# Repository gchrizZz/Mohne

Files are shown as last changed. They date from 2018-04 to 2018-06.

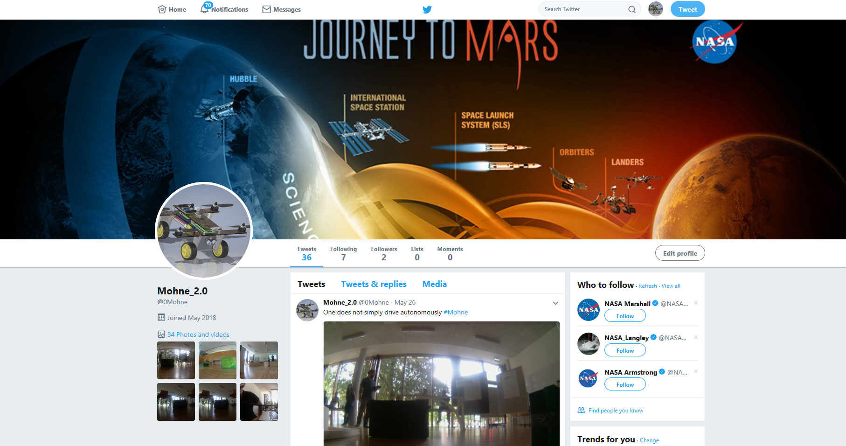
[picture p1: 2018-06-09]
01_Projektmanagement/Abschlussbericht/Screenshots/Twitter_Screenshot.PNG

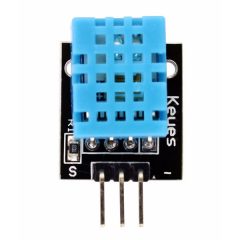
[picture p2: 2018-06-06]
04_Elektrik/KY-015_temperature_humidity_sensor_module-240x240.jpg

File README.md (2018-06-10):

# Mohne

Über dieses gitrepository können wir parallel am "Mohne für NASA" - Projekt arbeiten.

Ordnerstruktur:
- 01_Projektmanagement:  Bereich für Bericht und Organisation
- 02_Quellcode:          Bereich für die Programmierung des Quadrocopters
- 03_Konstruktion:       Bereich für die CAD-Teile des Quadrocopters 
- 04_Elektrik:           Bereich für Platinenlayouts und Circuits
- 05_Simulation:         Bereich für Circuit und Code der Simulation
- 06_Click-Dummy         Bereich für Click-Dummy für Web und App
- 99_Archiv:             Bereich für Ablage und nicht mehr relevante Artefakte

CAD Modell von Mohne:


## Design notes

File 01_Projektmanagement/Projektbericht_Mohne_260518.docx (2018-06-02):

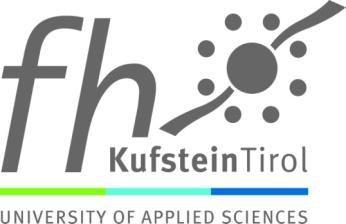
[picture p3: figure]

Project Data Explorer - Mohne

Projektbericht

Entwicklung eines Fahrzeugs für autonome/ ferngesteuerte Datenerfassung inklusive der Umweltbedingungen

Eingereicht bei:

Fachhochschule Kufstein Tirol Bildungs GmbH

Studiengang Smart Products & Solutions

Verfasser:

Anna Duregger, Christian Gruber, Christoph Jungwirth, Maximillian Möbes, Ludwig Paula, Markus Wiesmüller

Abgabedatum:

10.06.2017

# List of Figures

# Es konnten keine Einträge für ein Abbildungsverzeichnis gefunden werden.

# List of Tables

Es konnten keine Einträge für ein Abbildungsverzeichnis gefunden werden.

# List of Abbreviation

# Kurzfassung

# Abstract

# 1. Conecpt Development

Aufgrund der im letzten Semester geschaffenen Basis wurde die „Mohne“ weiterentwickelt. Alternativ gab es noch die Idee ein einfaches Auto zu konstruieren um damit die Anforderungen zu erfüllen. Letztendlich wurde die Entscheidung zugunsten der bereits gebauten Drohen getroffen und wir auf dieser Basis weiterentwickeln werden.

Für das neue Projekt wurden die folgenden Kriterien des Lektoren Teams gestellt:

- Eigenschaften des Fahrzeuges: Fahrmodus, Telemetriedaten erfassen und übertragen
- Datenerfassung: Umweltbedingungen permanent erfassen
- Digitaler Zwilling in MATLAB: Fahrzeug (mechanisches Modell-Kräfte)
- Simulation: Rapsberry Pi und Arduino Simulator
- Tracks: ferngesteuert und autonom

Die obenstehenden Punkte werden im nachfolgenden Bericht detailliert erläutert und darauf eingegangen.

## 1.1 Konzept der Fahrmodi

Die beiden Konzepte der Fahrmodi bestehen aus den Modi autonom Fahren und ferngesteuertes Fahren.

Bei der Aufgabenstellung autonomes Fahren – Obstacle Detection - sind die Anforderungen folgende:

- Eindeutige markierte Hindernisse müssen umfahren werden
- Die Hindernisse müssen abfotografiert werden
- Es werden keine Begrenzungswände verwenden
- Startpunkt lieg bei (0,0)
- Endpunkt wird vorgegeben
- Erfassen der Daten der verbauten Sensoren via ThingsSpeak und MathLab

Beim ferngesteuerten Fahren - Datenerfassung sind folgende Anforderungen:

- Startpunkt bei (0,0)
- Abfolge von Messfeldern wird je Team vorgegeben
- Hindernisse müssen umfahren werden
- Explorer wird ferngesteuert (Eingabegerät offen; Eingabe von Koordinaten, Steuerbefehle mittels Joystick)
- Erfassen der Daten der verbauten Sensoren via ThingsSpeak und MathLab

### 1.1.1 autonom

### 1.1.2 ferngesteuert

## 1.2 Fahrzeugaufbau

### 1.2.1 Elektronik

### 1.2.2 Software

# 2. Model Based Analytics

## 2.1 Digitaler Zwilling

# 3. Simulation

## 3.1 Pi Simulation

## 3.2 Arduino Simulation

# 4. Datenübertragung

## 4.1 Thinkspeak

## 4.2 Auswertung

# 5. Visualisierung MATLAB

## 5.1 Karte mit Fahrstrecke

## 5.2 Karte mit Messpunkte

## 5.3 Fahrstrecke mit Messungen

# 6. Rohdaten/Datalog

## 6.1 Timestamp+Daten

# 7. Es wird doch alles anderst als geplant

# 8. Zusammenfassung

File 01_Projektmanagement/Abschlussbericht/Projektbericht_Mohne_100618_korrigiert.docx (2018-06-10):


Project Data Explorer - Mohne

Projektbericht

Entwicklung eines Fahrzeugs für autonome / ferngesteuerte Datenerfassung inklusive der Umweltbedingungen

Eingereicht bei:

Fachhochschule Kufstein Tirol Bildungs GmbH

Studiengang Smart Products & Solutions

Verfasser:

Anna Duregger, Christian Gruber, Christoph Jungwirth, Maximillian Möbes, Ludwig Paula, Markus Wiesmüller

Abgabedatum:

10.06.2018

# List of Figures

IV

# Kurzfassung

V

Nachdem im letzten Jahr der erste Versuch gestartet war ein unbemanntes Fahrzeug auf den Mars zu schicken, ist die Mohne dieses Jahr weiterentwickelt worden. Die Aufgabe war es, das vorhandene Model weiterzuentwickeln und mit entsprechenden Modifikationen zu versehen. Dies ist in Form von Sensoren geschehen, welche Daten von der Oberfläche, der Umgebung und der Atmosphäre sammeln sollten. Damit die im ersten Projekt gestartete Idee nicht umsonst gewesen ist, wurde nach langer Diskussion entschieden, die Mohne 2.0 zu bauen. Um diese Annahme zu bestätigen, hat das Team unterschiedliche Designvarianten in Betracht gezogen. Das am Ende gewählte Design war ein sehr schlichtes und funktionales Design, welches entsprechend für die schwierigen und nicht vorhersehbaren Situationen auf dem Mars angepasst worden ist. Das Projektmanagement wurde gleich wie das im ersten Projekt (ein traditioneller Ansatz für die Gesamtplanung und für eine agile Methodik bei den Einzelaufgaben) gewählt. Um die benötigten Komponenten herzustellen – die Teile wurden überarbeitet und weiterentwickelt – konnten die Geräte im FabLab in Wattens genutzt werden. Um die Tauglichkeit für einen Einsatz auf dem Mars zu gewährleisten, mussten entsprechende Aufgaben auf einer Teststrecke bewältigt werden. Hierbei gab es einen Parcours, der mit Hilfe einer manuellen Steuerung sowie autonom befahren werden musste. Kurz vor Ende der Testphase hatten wir technische Probleme (ein notwendiges elektrisches Bauteil ist verschließen) und mussten unser komplettes Konzept innerhalb weniger Stunden den neuen Gegebenheiten anpassen und ein „neues“ Fahrzeug entwickeln.

# Abstract

VI

After last year's first attempt to send an unmanned vehicle to Mars, the Mohne has been further developed this year. The task was to further develop the existing model and provide it with appropriate modifications. This has been done in the form of sensors that should collect data from the surface, the environment and the atmosphere. So that the idea started in the first project was not in vain, after a long discussion it was decided to build the Mohne 2.0. To confirm this assumption, the team considered different design variants. The design chosen at the end was a very simple and functional design, which has been adapted accordingly for the difficult and unpredictable situations on Mars. Project management was chosen in the same way as in the first project (a traditional approach to overall planning and an agile methodology for the individual tasks). The devices could be used in the FabLab in Wattens to provide the required components - the parts were reworked and further developed. In order to ensure the suitability for a mission on Mars, corresponding tasks had to be mastered on a test track. There was a course which had to be driven with a manual control and autonomous. Shortly before the end of the test phase we had technical problems (a necessary electrical component is closed) and had to adapt our complete concept within a few hours to the new conditions and develop a "new" vehicle.

# 1. Concept Development

Aufgrund der im letzten Semester geschaffenen Basis wurde die „Mohne“ weiterentwickelt. Alternativ gab es noch die Idee ein einfaches Auto zu konstruieren um damit die Anforderungen zu erfüllen. Letztendlich wurde die Entscheidung zugunsten der bereits gebauten Drohne getroffen, die das Projektteam auf dieser Basis weiterentwickeln wird.

Für das neue Projekt wurden die folgenden Kriterien des Lektoren Teams gestellt:

- Eigenschaften des Fahrzeuges: Fahrmodus, Telemetrie Daten erfassen und übertragen
- Datenerfassung: Umweltbedingungen permanent erfassen
- Digitaler Zwilling in MATLAB: Fahrzeug (mechanisches Modell-Kräfte)
- Simulation: Raspberry Pi und Arduino Simulator
- Tracks: ferngesteuert und autonom

Die obenstehenden Punkte werden im nachfolgenden Bericht detailliert erläutert und besprochen.

## 1.1 Konzept der Fahrmodi

Die beiden Konzepte der Fahrmodi bestehen aus den Modi autonom Fahren und ferngesteuertes Fahren.

Bei der Aufgabenstellung autonomes Fahren - Obstacle Detection - sind die Anforderungen wie folgt:

- Eindeutige markierte Hindernisse müssen umfahren werden
- Die Hindernisse müssen abfotografiert werden
- Es werden keine Begrenzungswände verwendet
- Startpunkt lieg bei (0,0)
- Endpunkt wird vorgegeben
- Erfassen der Daten der verbauten Sensoren via ThingsSpeak und MATLAB

Beim ferngesteuerten Fahren - Datenerfassung gibt es folgende Anforderungen:

- Startpunkt bei (0,0)
- Abfolge von Messfeldern wird je Team vorgegeben
- Hindernisse müssen umfahren werden
- Explorer wird ferngesteuert (Eingabegerät offen; Eingabe von Koordinaten, Steuerbefehle mittels Joystick)
- Erfassen der Daten der verbauten Sensoren via ThingsSpeak und MATLAB

### 1.1.1 Autonom

Um den Parcours autonom zu absolvieren wurden zusätzliche Sensoren verwendet, mit denen diese Aufgabe vereinfacht wird. Zum einen wurde ein Gyroskop angeschlossen um die Orientierung im Raum zu vereinfachen. Zum anderen ein Ultraschallsensor damit Hindernisse erkannt werden können.

Für die Programmierung wurde der Raspberry Pi und der Arduino verwendet. Auf dem Arduino ist die Motorsteuerung gespeichert und auf dem Pi die Kamerafunktion und der Array. Beide Computer kommunizieren mithilfe einer i2c-Verbindung und senden Zahlen hin und her, welche die verschiedene Funktionen auslösen. Das autonome Fahren beim Auto konnte leider nicht komplett absolviert werden, da das Auto selber nicht in einer Linie fährt, sondern eine Rechtsneigung besaß. (defekter Reifen) Es fuhr so lange vorwärts, bis sich ein Hindernis 30 Zentimeter vor dem Fahrzeug befindet. Dieser Wert wird mit einem Ultraschallsensor berechnet. Dieser ist am Arduino angeschlossen und muss dem Raspberry Pi mitteilen, dass ein Hindernis vorhanden ist und ein Foto gemacht werden muss. Durch die i2c-Verbindung wird vom Arduino die Zahl 7 versendet. Das Problem hierbei ist, dass der Arduino nicht von sich aus in der Slave Konfiguration Zahlen senden kann. Somit muss der Raspberry Pi regelmäßig den Arduino fragen, ob ein Hindernis vorhanden ist. Diese Frage wird mithilfe einer Zahl jede Sekunde gestellt und geantwortet wird mit einen von zwei Zahlen. Entweder ist ein Hindernis vorhanden oder die Bahn ist frei. Nachdem der Raspberry Pi die Antwort erhalten hat, wird entsprechend gehandelt. Bei einem Objekt wird die Kamerafunktion ausgelöst und das Bild wird auf Twitter geladen. Nachdem das Foto geschossen wurde, wird eine Rechtskurve gefahren und das Auto fährt weiter.

Die Motorsteuerung wurde aus dem 1. Projekt im 1. Semester übernommen und angepasst. Um Platz auf dem Breadboard und Pins auf dem Arduino zu sparen wurde nur eine H-Brücke gebaut und die linken bzw. rechten Reifen parallelgeschaltet. Da die Motoren sehr schwach sind, wurde immer der höchste Wert von 255 verwendet. Bei den Links- und Rechtsdrehungen wird wie ein Panzer gefahren. Das heißt, dass beide Seiten sich gegeneinander bewegen, bis sich das Auto in einem Winkel von 90 Grad gedreht hat.

### 1.1.2 Ferngesteuert

Bei der Aufgabe das Fahrzeug über den Parcours per Fernsteuerung zu fahren gibt es viele Möglichkeiten die Fernsteuerung zu kreieren. Wir haben uns dann schlussendlich für die Laptoptastatur entschieden. Dies hat den Vorteil, dass jeder den Code testen kann ohne eine physische Fernsteuerung mitnehmen zu müssen und falls es Probleme bei der Verbindung gibt, kann die Mohne per Not-Stopp ausgeschaltet werden. Da das Fahrzeug bereits mit einem Samba Server verbunden ist war die Remote-Steuerung leicht zu verwenden und in der Testphase konnten die verschiedenen Programme schnell verändert werden. Der Code für die Fernsteuerung heißt ‚FernFoto.py‘ und kommt von ‚Fernsteuerung‘ und ‚Foto‘.

Die Motorsteuerung war auf dem Arduino gespeichert. Dies war bei der ursprünglichen Mohne, wie auch bei unserem endgültigen Auto der Fall. Auf die Motorsteuerung selber wurde bereits im Abschnitt Autonom eingegangen.

Der Code für die Fernbedienung wurde auf dem Raspberry Pi mithilfe eines Keyloggers geschrieben. Der verwendete Logger kommt aus der pynput Library. Dies hatte den Vorteil, dass es auch eine Key Release Funktion gab und dadurch die Mohne stoppt, wenn eine Taste losgelassen wurde. Der Nachteil war allerdings, dass der Keylogger nicht zusammen mit Schleifen funktioniert. Somit konnte der Raspberry Pi nicht selbständig Fotos schießen. Dieses Problem wurde gelöst indem ein separater Tastendruck die Kamera auslöst und das Bild auf Twitter hochgeladen wird.

Die Mohne wird klassisch mit den Pfeiltasten gesteuert. Beim Drücken der Leertaste entsteht das Foto und mit der Escape-Taste wird das Programm gestoppt. Wenn keine Taste gedrückt wird oder eine losgelassen wird, werden die Motoren ausgeschaltet.

Jetzt müssen die Befehle nur noch an den Arduino geschickt werden, um diese auszuführen Die im Unterricht gelernte i2c-Verbindung wurde verwendet und modifiziert. Jede Taste wurde einer Zahl zugeordnet, die an den Arduino geschickt wird. Wenn die Motoren stoppen sollen wird auch eine Zahl gesendet.

Der Code auf dem Arduino heißt ‚Fern_1.0‘. Auf diesem wurden bereits Klassen für die jeweiligen Richtungen geschrieben. Also vorwärts, rückwärts, rechts und links. Dazu natürlich noch die Stopp Funktion. Durch die i2c-Verbindung wartet der Arduino auf die Zahlen, welche vom Raspberry Pi gesendet werden. Bei der Zahl 1 wird nach vorne gefahren, bei der 2 nach rechts. Wird die 3 gesendet nach Links und bei der 4 rückwärts. Die Nummer 5 wird für die Stopp-Funktion verwendet.

Die Fernsteuerung lief trotz vielen Schnittstellen sehr präzise und ohne Verzögerung.

## 1.2 Fahrzeugaufbau

### 1.2.1 CAD als Unterstützung für die Fertigung und Designentwicklung

Die Mohne besteht aus 66 Einzelteilen. Kabel, Schrauben, Muttern und Kabelbinder sind hierbei nicht berücksichtigt.

In Abbildung 1 ist das fertige CAD Modell als Explosionsdarstellung aufgezeigt, um die Komplexität des Modells zu veranschaulichen.

Ohne ein ausgereiftes CAD-Modell ist eine ordnungsgemäße Fertigung der Mohne nicht möglich. Außerdem hilft das digitale Modelle etwaige Lücken bzw. Versäumnisse in der Konzeption aufzudecken, noch bevor eine zeitintensive Fertigung gestartet wird.

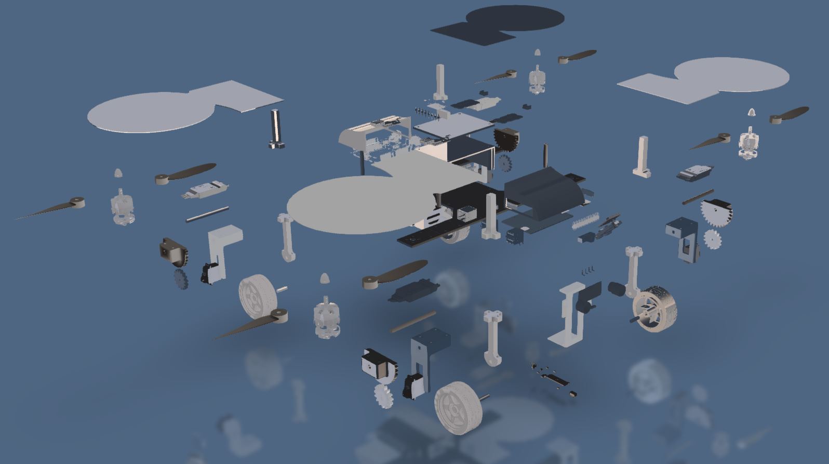
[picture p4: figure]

Abbildung 1: Explosionsdarstellung Mohne

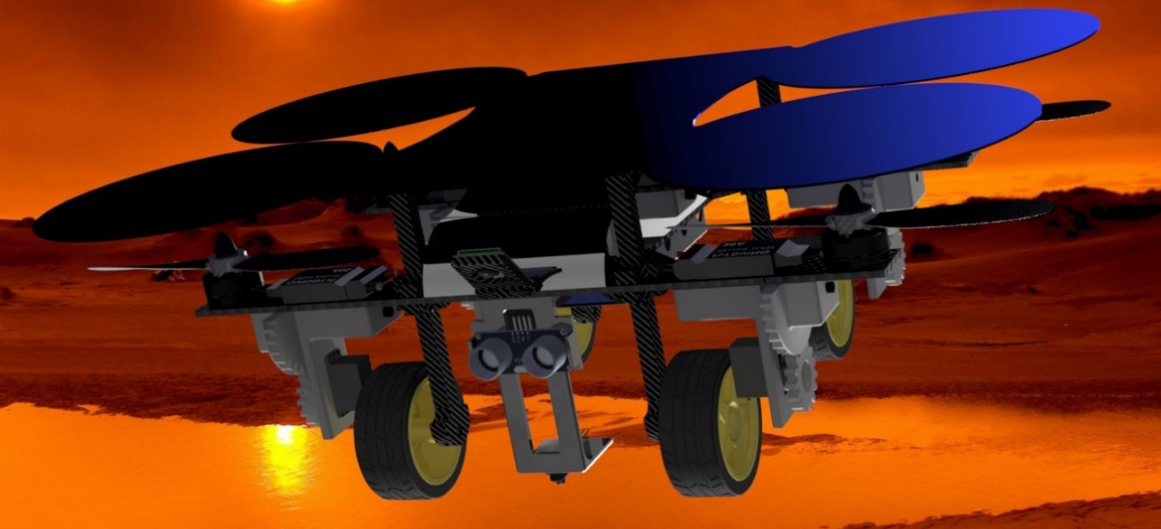
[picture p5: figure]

Abbildung 2: Rendering Ansicht Mohne

Abbildung 2 zeigt ein Rendering Bild der auskonstruierten Mohne. Im Zuge der Designentwicklung wurden folgende vier Designschwerpunkte hinsichtlich der NASA als Kunde getroffen:

1. Entwicklung eines individuellen und additiv gefertigten Gehäuses zum Schutz der Steuergeräte
2. Modulares Sensorplattenkonzept, welches einen Wechsel durch reine Schraub- und Steckverbindungen ermöglicht
3. Einsatz von Kohlefaser als modernes, vielseitiges und gewichtsoptimiertes Material
4. Solarmodule zum Laden des Akkumulators

Das gesamte CAD Modell und das Designkonzept kann unter https://github.com/gchrizZz/Mohne abgerufen werden.

### 1.2.2 Elektronik

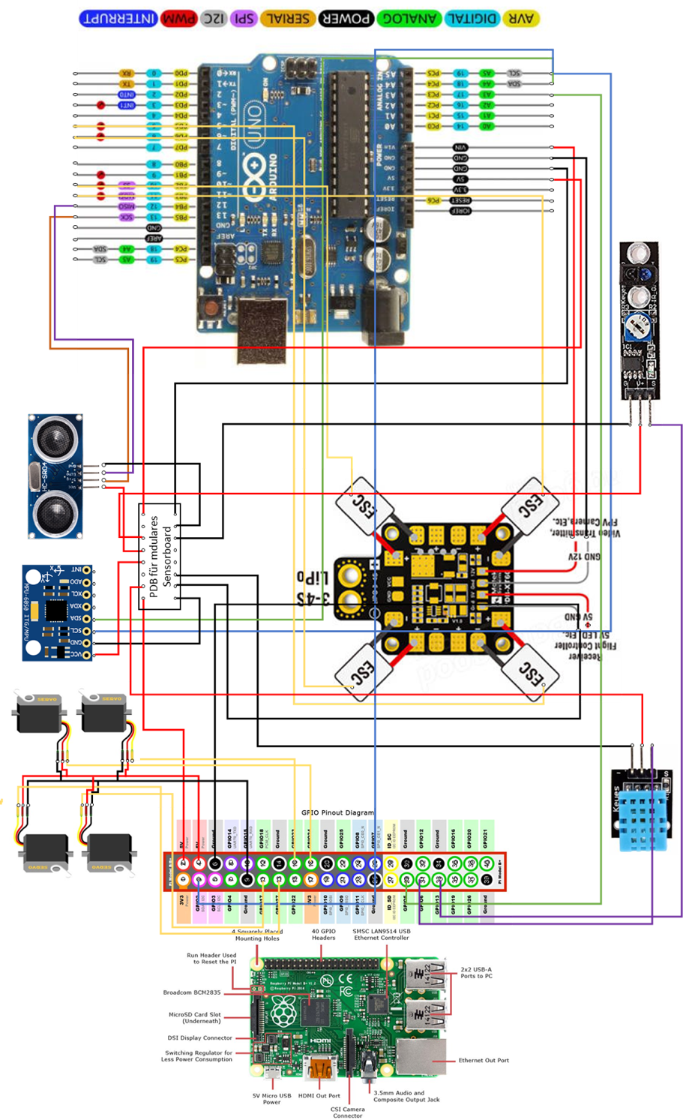
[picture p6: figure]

Abbildung 3: Elektronische Komponenten und Verkabelung Mohne

Abbildung 3 zeigt den Kabelbaum und die elektrischen Komponenten der Mohne auf. Dieser Plan berücksichtigt lediglich die geforderten Sensoren, dennoch ist die Designentscheidung einer modularen Sensorplatte bereits einkalkuliert. Hierfür wurde ein gesondertes PDB ausschließlich für die Stromversorgung aller angebrachten Sensoren eingearbeitet. Somit müssen zusätzliche Sensoren lediglich an diesem PDB und mit Ihren Signalkabeln an das vorgesehene Steuergerät (Pi oder Uno) angeschlossen werden. Löten ist nicht mehr notwendig.

### 1.2.3 Kommunikation

Der Zugriff der Mohne wird nach wie vor über einen Samba Server realisiert. Samba ist ein freies Programmpaket, das es ermöglicht, Windows-Funktionen wie die Datei und Druckdienste unter anderen Betriebssystemen zu nutzen und die Rolle eines Domain Controllers anzunehmen. Es implementiert hierfür unter anderem das Server Message Block/Common Internet File System-Protokoll (SMB/CIFS-Protokoll). Im Projekt wurde Samba als DC und DNS verwendet, damit man via RDP über WLAN auf den Raspberry Pi zugreifen kann, ohne eine statische IP hinterlegen zu müssen. Der Hostname der Drohne lautet „Mohne“.

Die Kommunikation zwischen dem MPU, dem Arduino Uno und dem Pi wurde via I²C realisiert. I²C (gesprochen "I quadrat C") ist ein synchroner, serieller Zweidraht-Bus, der jeweils eine bidirektionale Daten- und Taktleitung verwendet und für die Kommunikation zwischen ICs über kleine Distanzen geeignet ist. Die Bezeichnung steht für IIC, Inter-Integrated Circuit.

Der Kombi-Sensor (KY-015), als auch der Linetracking Sensor (KY-033) sind mittels jeweils einem GPIO Pin mit dem Pi verbunden. Somit können die Daten von diesen direkt über das digitale Eingangssignal am Pi verarbeitet werden.

Da die Logikverarbeitung für das autonome Fahren hinsichtlich Linetracking und Orientierung in einem Schachbrett-Array auf dem Pi abläuft, kann man mit dieser einfachen und direkten Kommunikation die Logik am leichtesten realisieren.

Die Servos, welche für die Ausrichtung der Motorhalterung an allen vier Armen der Drohne verantwortlich sind, werden ebenfalls via GPIO Pins an den Raspberry Pi angebunden. Jedoch wird diesen ein imitiertes PWM Signal gesendet, um sie zu steuern.

Der Ultraschallsensor (USS) ist mittels zwei IO Pins direkt am Arduino angeschlossen. Auf diesem Weg kann die unmittelbare Hinderniserkennung am schnellsten realisiert werden. Da der USS ausschließlich mit dem Arduino Uno kommuniziert, muss die Logikverarbeitung hierfür im C++ Code auf dem Arduino stattfinden.

## 1.3 Model Based Analytics

Der Grundgedanke von Model Based Analytics ist die virtuelle bzw. digitale Darstellung eines physischen Modells. Dieses Modell wird in der digitalen Welt analysiert und interpretiert. Dies ist eine Methode gewisse Problemstellungen virtuell darzustellen und diese als Simulation zu verwenden.

Für unser Projekt wurde der Digitale Zwilling gewählt um diese Problemstellung darzustellen und eine entsprechende Lösung zu finden.

## 1.4 Digitaler Zwilling

Das Konzept eines digitalen Zwillings besteht aus drei Elementen: einem physischen Zwilling in der realen Welt, einem digitalen Zwilling im virtuellen Raum, der sowohl alle alten betrieblichen Daten als auch die Echtzeitdaten des physischen Zwillings abbildet, und die Interkonnektivität, die es den Zwillingen ermöglicht, die Informationen auszutauschen. Digitale Zwillingen können für Simulationen verwendet werden und für Einblicke in den arbeitenden Zwilling, um Prozesse zu überwachen und mögliche Fehler zu entdecken.[^1]

Im folgenden Abschnitt werden nähere Beschreibungen zum digitalen Zwilling angeführt.

### 1.4.1 Allgemein

Ein digitaler Zwilling ist eine virtuelle Modellbildung zum Beispiel eines Prozesses, eines Produkts oder einer Dienstleistung, welches die reale und virtuelle Welt verbindet. Digitale Zwillinge verwenden reale Daten von installierten Sensoren, welche die Arbeitsbedingungen oder Position von Maschinen repräsentieren. Diese Kopplung der virtuellen und realen Welten ermöglicht die Analyse von Daten und die Überwachung von Systemen, um Probleme verstehen und bearbeiten zu können, bevor sie überhaupt auftreten. Ausfallzeiten können frühzeitig vermieden werden und dadurch neue Chancen entwickeln und mithilfe von Computersimulationen, damit die Zukunft besser geplant werden kann. Heutzutage werden digitale Zwillinge eine geschäftliche Notwendigkeit, weil der gesamte Lebenszyklus eines Produkts, Prozesses oder Geschäftsmodells abdeckt werden kann und somit die Grundlage für verbundene Produkte und Dienstleistungen bilden.

Für den sogenannten digitalen Zwilling sind folgende Anforderungen notwendig: das abzubildende reale Objekt, den digitalen Zwilling im virtuellen Raum und Informationen, welche die beiden miteinander verbinden. Digitale Zwillinge können dadurch die operative und auch finanzielle Leistungsfähigkeit eines Objekts wie einer Anlage oder einer Dienstleistung verbessern und in Echtzeit dargestellt werden.

In der ersten Phase „Design“ geht es um den Umgang mit komplexen Produktanforderungen, schnellen Entwicklungszyklen und strengen regulatorischen Anforderungen. In der zweiten Phase „Erstellung (manufacturing)“ kann der Zwilling helfen, bessere Effizienz, Qualität und höheren Ertrag in der Erstellung zu erreichen. In der dritten Phase „Nutzung (operate)" kann ein digitaler Zwilling u. A. eingesetzt werden, um die Verfügbarkeit von Objekten (z. B. Maschinen) zu verbessern. In der vierten Phase „Wiederverwertung (Recycling)“ kann der digitaler Zwilling z.B. für die Ersatzplanung oder der Eruierung von Upcycling-Potenzialen eingesetzt werden.

### 1.4.2 Projektbezogen

Unser Plan B des Projektes Data Explorer wurde an einem Tag zu einem Auto umgebaut und deren Funktionen erweitert bzw. ergänzt. Am Auto herrscht ein mechanisches Kräftemodell, welches im folgenden Kapitel dargestellt wird. Dadurch haben wir entschieden, dass wir die Kraft des Motors mit der Beschleunigung als Digitalen Zwilling modellieren bzw. darstellen wollen. Interessant an der Darstellung wird, wie sich die Beschleunigung „a“ während der Datenerfassung verhält. Die Erfassung der Daten erfolgt mithilfe der Matlab Software und dessen Mobile App. Durch die Kommunikation zwischen den beiden Anwendungen kann eine Erfassung der Daten mit verschiedenen Sensoren, wie Beschleunigungssensor, erfasst werden. Es kann analysiert werden, ob bei der Absolvierung des vorgegebenen Parcours eine Verminderung der Beschleunigung eintritt, wenn ein Hindernis kommt oder eine Kurve nach links oder rechts gemacht wird. Der digitale Zwilling wird in einem Plot der Matlab Software dargestellt, damit das Diagramm entsprechend erläutert und interpretiert werden kann.

### 1.4.3 Material und Methoden

Für die Erfassung des digitalen Zwillings unseres Sommerprojektes haben wir uns entschieden, dass wir die Anwendung der Matlab App verwenden werden, da wir kein Logfile über den Raspberry Pi erstellen. Für die Anwendung ist die Matlab Software und der Download der dazugehörigen Matlab Mobile App notwendig. Zu Beginn wird die Matlab Mobile App am Smartphone installiert, egal ob Android oder iOS Betriebssystem. Am Smartphone können die unterschiedlichsten Sensoren wie Beschleunigungs-, Magnetfeld-, Positions-, Winkelgeschwindigkeits- und Orientierungssensor aktiviert werden. In der Software ist eine Installation eines Add-Ons zu erledigen. Um eine Verbindung zwischen der Software und der App herzustellen, wird in der Kommandozeile der Software der Konnektor aktiviert. Es wird nun die funktionierende IP-Adresse angezeigt, welche im Smartphone eingegeben wird, um eine Kommunikation herstellen zu können. Als nächsten Schritt wird der Link von PC und Smartphone erzeugt und es können sowohl am Smartphone und in der Kommandozeile durch bestimmte MATLAB-Befehle die Sensoren aktiviert werden. Für eine korrekte Datenerfassung werden durch Befehle in der Kommandozeile die Datenaufnahme der Messwerte aktiviert und auch wieder beendet. Mit den erfassten Sensordaten des Smartphones können die Daten auf verschiedensten Arten analysiert und auch dargestellt werden. Die Daten können in einem Diagramm inklusiver Legende in MATLAB dargestellt werden.

### 1.4.4 Mechanisches Modell des Fahrzeuges

Im folgenden Bild wird das mechanische Modell unseres Fahrzeuges abgebildet. Das Kräftemodell des Fahrzeuges besteht aus der Reibungskraft, der Erdanziehungskraft, der Kraft des Motors in der Vorwärtsbewegung und der Kraft des Autos.

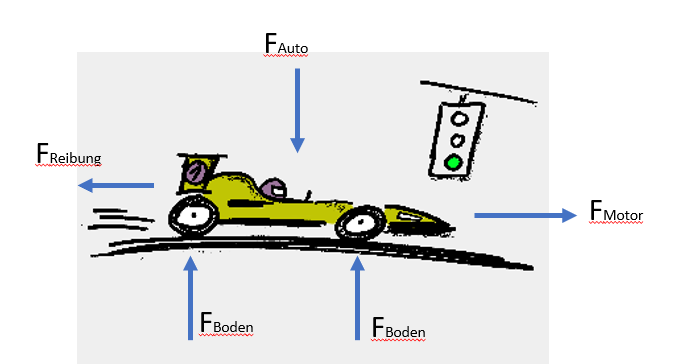
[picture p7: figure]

Abbildung 4: Mechanisches Kräftemodell des Autos

### 1.4.5 Ergebnisse

Aus der Datenerfassung der Matlab App konnte die Kraft des Motors erfasst und gemessen werden. Die Daten wurden während unseres autonomen Fahrens, welches leider in der kurzen Zeit nicht möglich war fertig zu programmieren, aufgenommen. Anhand der Daten, die auf die Software von Matlab übertragen wurden, kann herausgelesen werden, dass unser Programm eine relativ kontinuierliche Geschwindigkeit durchfährt. Daraus resultiert, dass unser Fahrzeug, wegen dem nicht fertigen ferngesteuertem Programm, nicht immer Objekte bzw. Hindernisse erkennen kann und somit sich nicht mit einer kontinuierlichen Geschwindigkeit fortbewegt.

Mit der Darstellung der Beschleunigung ist keine kontinuierliche Beschleunigung ersichtlich. Der programmierte Code enthält leider keine konkrete Struktur bzw. Abfolge und somit resultiert ein relativ hektisches Beschleunigungsdiagramm. In der Mitte des Diagramms kann man erkennen, dass das Fahrzeug einen Stillstand hat und womöglich ein Hindernis erkennen konnte.

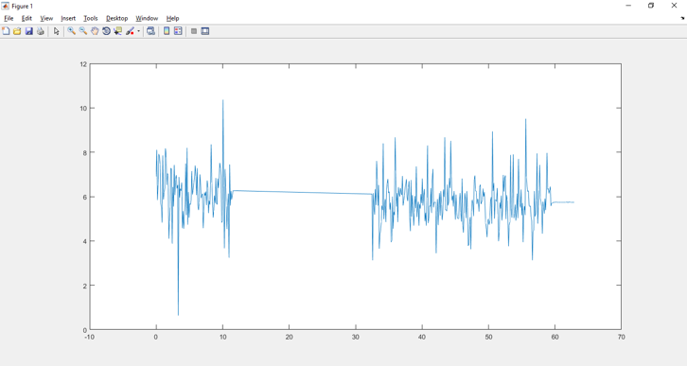
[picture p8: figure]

Abbildung 5: Diagramm für die Beschleunigung

Im folgenden Plot von Matlab ist die Winkelgeschwindigkeit dargestellt. Auf dieser Darstellung erkennt man wie sich das Fahrzeug in den Richtungen verändert. Wie schon vorher erläutert haben wir den Fernsteuerungsmodus leider nicht bis zum Ende programmieren können. Im Diagramm ist schön zu sehen, wie oft und schnell das Fahrzeug die Richtung ändert. Das ist der Grund, dass das Programm nicht in der Zeit fertig geworden ist. Deswegen fährt das Fahrzeug willkürlich durch den Raum und während der Gerade des Diagramms hat es angehalten, weil es womöglich ein Hindernis erkannt hat. Ursprünglich ist es gedacht, dass das Fahrzeug einem Hindernis ausweicht, jedoch nach dem Diagramm sind auf unserem vorgegebenen Parcour sehr viele Hindernisse platziert worden.

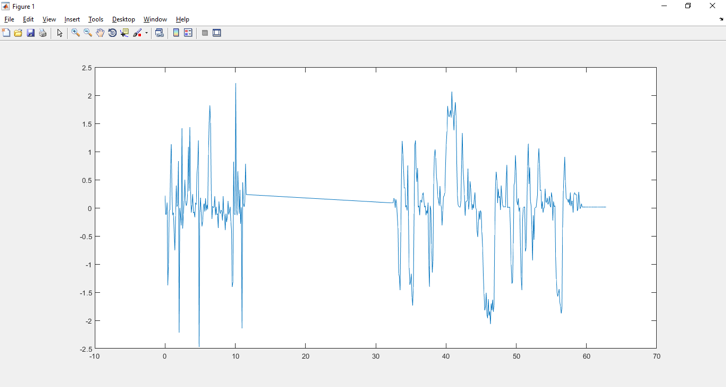
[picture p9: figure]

Abbildung 6: Diagramm für die Winkelgeschwindigkeit

### 1.4.6 Konklusion

Am Beispiel der beiden Diagramme kann man erkennen, dass unser programmierter Quellcode leider nicht dem Fernsteuerungsmodus entspricht. Das Fahrzeug kann durch die Bilderkennung nicht kontinuierlich die Hindernisse erkennen und daraufhin die Geschwindigkeit reduzieren bzw. nach dem Stillstand wieder beschleunigen. In der Mitte des Diagramms ist ein Stillstand zu erkennen, weil hier womöglich ein Hindernis erkannt wurde. In beiden Abbildungen ist die Beschleunigung als auch die Winkelgeschwindigkeit sehr hektisch, da das Programm aus zeitlichen Gründen nicht fertig geschrieben werden konnte.

# 2. Simulation

Simulation ist die Nachahmung des Betriebs eines realen Prozesses oder Systems. Der Akt der Simulation erfordert zunächst die Entwicklung eines Modells, das die wesentlichen Merkmale, Verhaltensweisen und Funktionen des gewählten physikalischen oder abstrakten Systems oder Prozesses darstellt. Das Modell stellt das System selbst dar, während die Simulation den Betrieb des Systems über die Zeit darstellt.

Simulation wird in vielen Bereichen eingesetzt, z.B. bei der Simulation von Technologien zur Leistungsoptimierung, Sicherheitstechnik, Tests, Schulungen und Videospielen. Mit Hilfe der Simulation können die tatsächlichen Auswirkungen alternativer Bedingungen und Vorgehensweisen aufgezeigt werden. Die Simulation wird auch verwendet, wenn das reale System nicht aktiviert werden kann, weil es möglicherweise nicht zugänglich ist, weil es gefährlich oder inakzeptabel ist, weil es entworfen, aber noch nicht gebaut wird, oder weil es einfach nicht existiert.

## 2.1 Arduino Simulation

Kernpunkte der Simulation sind die Erfassung valider Quelleninformationen über die relevante Auswahl der wichtigsten Merkmale und Verhaltensweisen, die Verwendung von vereinfachenden Annäherungen und Annahmen innerhalb der Simulation sowie die Treue und Validität der Simulationsergebnisse.

Bezogen auf das Projekt, war die Anforderung die Simulation eines IoT-Systems, weshalb der Arduino mit zwei Sensoren und einem Aktor simuliert wurde, um ein wesentliches Abbild der Funktionen der Mohne zu bekommen.

Die genaue Simulation der Mohne ermöglichte die sichere und effiziente Entwicklung von Regelalgorithmen. Darüber hinaus ermöglicht es die Erfassung der Umgebung mit Hilfe des Ultraschall - und Temperatursensors und erlaubt es, wiederholbare Experimente zu entwerfen. Die gewählte Simulationsumgebung ist Autodesk Tinkercad, die es ermöglicht, physikalisch realistische Simulationen für Arduino zu erstellen. Da am Vortag der Projektvorstellung die Mohne zu einem fahrtüchtigen Auto umgebaut werden musste, wurde keine separate Simulation für das Auto erstellt – die Funktion und Verhaltensweise der Sensoren kann jedoch nahezu Eins zu Eins auf das Auto übertragen werden.

### 2.1.1 Sensorsimulation

Der Tinkercad Simulator verfügt über zahlreiche Sensoren die jedoch nicht exakt die gleichen wie die real verbauten sind, allerdings deren Funktion wiederspiegeln. Wie bereits erwähnt und in Abbildung 7 ersichtlich, wurden der Ultraschallsensor und der Temperatursensor simuliert. Der Temperatursensor misst dabei ständig die Umgebungstemperatur, welche sich über ein Potentiometer verändert werden kann, indem die Spannung verändert wird, um die sich verändernde Umgebungstemperatur zu simulieren. Da die Messdaten des Fahrzeuges an ThingSpeak übertragen und dort visualisiert werden sollen, wird die Darstellung der Messdaten in der Simulation über ein 16 x 2 LCD-Display realisiert.

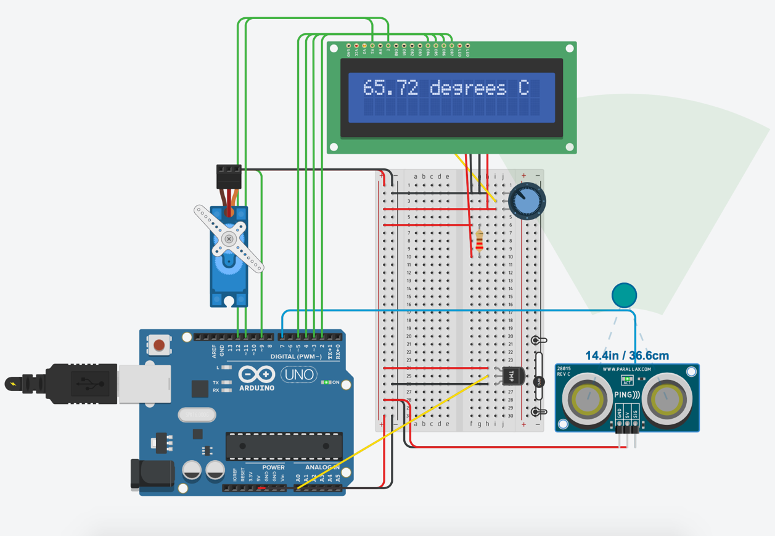
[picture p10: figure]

Abbildung 7: Aufbau Simulation Arduino

Ursprünglich sollte der Bremsvorgang erfolgen, indem das hintere Propellerpaar für den Vorschub der Mohne verantwortlich ist, das hintere Propellerpaar stoppt, sobald ein Hindernis erkannt wird und das vordere Propellerpaar die Mohne abbremst, bis diese ausrollt und schließlich vor dem Hindernis zum Stehen kommt. In der Simulation wird diese Idee mit Hilfe eines Ultraschallsensors und einem Servo umgesetzt.

Der Ultraschallsensor erkennt ob und in welchem Abstand sich vor dem Fahrzeug ein Hindernis befindet (Abbildung 8). Wird ein Hindernis im Abstand von < 50 cm erkannt, wird der Bremsvorgang wie bereits beschrieben eingeleitet. Die Umlenkung des Schubes entgegen der Bewegungsrichtung zum Abbremsen der Mohne wird dadurch simuliert, indem der Servo, sobald der Ultraschallsensor ein Hindernis erkennt, sich um 180° dreht.

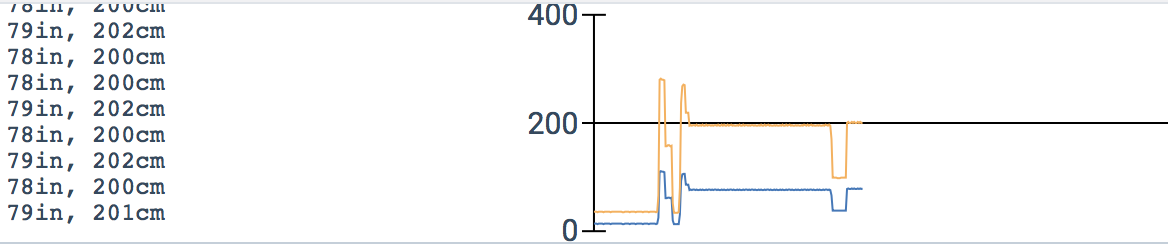
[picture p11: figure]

Abbildung 8: Abstandsmessung Ultraschallsensor

### 2.1.2 Vergleich simulierter und realer Ergebnisse

In der Simulation wurde für die Temperaturmessung ein TMP 36 Temperatursensor verwendet. Dies ist ein Niederspannungs-Temperatursensor mit Präzisions-Temperaturmessung über den Temperaturbereich -40°C bis +125°C. Er liefert eine Spannungsausgabe, die linear proportional zur Celsius-Temperatur ist. Wirklich verbaut wurde jedoch ein KY-015 Kombi Sensor Temperatur und Feuchtigkeit. Vorteil dieses Sensors ist die Kombination von Temperaturmessung und Luftfeuchtigkeitsmessung in einer kompakten Bauform. Der Messbereich für die Temperatur erstreckt sich allerdings nur von 0 bis +50°C. Da jedoch bei Raumtemperatur gemessen wurde, gibt es keine Unterschiede zwischen simulierter und realer Temperatur. Auch die simulierte Funktionsweise und Ergebnisse des Ultraschallsensors unterscheiden sich nicht vom real verbauten Sensor. Unterschiede zwischen Simulation und realer Umsetzung besteht in der Darstellung der Messergebnisse. Während die gemessene Temperatur in der Simulation über ein LCD-Display ausgegeben wird erfolgte die Datenübertragung und Darstellung wie unter Abschnitt 4 beschrieben. Ob sich der Bremsvorgang, wie in der Simulation gedacht, realisieren hätte lassen kann nicht beurteilt werden, da die Mohne zu einem Auto umfunktioniert werden musste, bevor der Bremsvorgang einmal durchgeführt werden konnte.

### 2.1.3 Schlussfolgerung

Die Simulation ist ein geeignetes Mittel um vereinfachende Annäherungen und Annahmen zu erfassen und hat in vereinfachter Form den komplexen Realaufbau wiedergespiegelt. In der Simulation konnte nicht exakt der Aufbau der Mohne, wie später realisiert, umgesetzt werden, da das Simulationsprogramm nur eine begrenzte Anzahl an Sensoren zur Auswahl stellt und auch nur einen Arduino simulieren lässt, für eine exakte Umsetzung jedoch auch ein Raspberry Pi benötigt wurde. Die Messergebnisse zeigen jedoch, dass auch eine vereinfachte Simulation sehr gute Ergebnisse liefert.

# 3. Datenübertragung

## 3.1 ThingSpeak

Der zentrale Teil der Anforderungen für das Projekt war die Übertragung von Messdaten der Fahrzeuge über das Web hin zu einer Cloudplattform, hier ThingSpeak. ThingSpeak ist eine Open IoT Platform (Cloudservice), die im Zusammenspiel mit MATLAB eine Menge Funktionen bietet, darunter auch die Übertragung von Messdaten. Dabei waren gewisse Parameter vorgegeben, andere wiederum waren, in einem bestimmten Rahmen, frei wählbar. Für die Übertragung der Daten kam sowohl das HTTP/REST-Protokoll als auch das MQTT-Protokoll in Frage. Die Entscheidung fiel zugunsten des MQTT-Protokolls, das speziell für embedded devices mit geringer RAM- und CPU-Leistung. Darüber hinaus verbraucht MQTT sehr viel weniger Bandbreite und eignet sich daher optimal für die Verwendung mit Arduino und Raspberry Pi. Zusätzlich gibt es die Möglichkeit, Nachrichten mit unsecured TCP zu senden, womit nochmal die Performance verbessert wird.

Um das Protokoll für die Übertragung der Messdaten zu nutzen, ist es erforderlich, eine entsprechende Library auf dem Raspberry Pi zu installieren, in diesem Fall die Paho Library.

In dem dazugehörigen Code <mqtt_Telemetrie_ThingSpeak_V3> sind einige Funktionen derzeit auf „False“ gesetzt, da sie einerseits die Übertragung der entsprechenden Nachricht auf anderen Wegen ermöglichen (statt UnsecuredTCP zum Beispiel UnsecuredWebsockets) oder das Ansprechen eines zweiten Channels auf ThingSpeak ermöglichen. Die Verbindung zu ThingSpeak ließ sich im Nachhinein relativ einrichten, vor allem da es auch in einer Übungsveranstaltung im Studienfach Datenübertragung vorgestellt wurde. Das eigentliche Übertragen der Telemetriedaten wird unter Punkt 7 bis 12 näher beschrieben.

## 3.2 Auswertung

Nach erfolgreichem Herstellen einer Verbindung zu ThingSpeak sollten nun die geforderten Daten aufgenommen und automatisch an ThingSpeak übertragen werden. Die CPU-Temperatur, RAM-Auslastung, Data Up- und Download werden vom Raspberry Pi selbst erfasst, im Gegensatz zu Luftfeuchtigkeit und Umgebungstemperatur, die über einen Kombisensor (KY-015) ausgelesen werden.

Für diesen Kombisensor muss eine spezielle Library von Adafruit installiert werden, Adafruit_DHT. Nach der Installation kann der Sensor ausgelesen werden, indem man einen entsprechenden GPIO-Pin definiert. Der Kombisensor gibt dann zuerst den Wert für die Luftfeuchte und dann den Wert für die Umgebungstemperatur aus. Die erfassten Werte für Luftfeuchte und Umgebungstemperatur können den Abbildungen 7 und 8 entnommen werden.

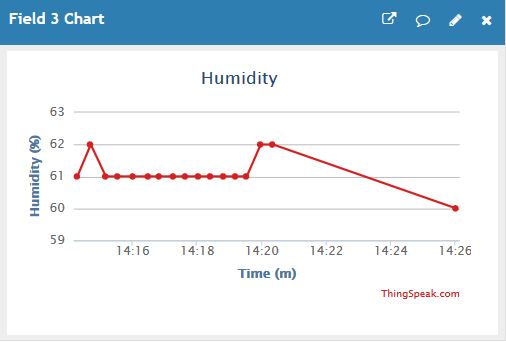
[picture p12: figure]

Abbildung 9: Luftfeuchtigkeit

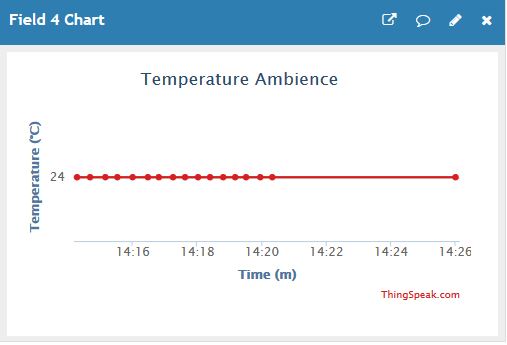
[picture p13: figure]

Abbildung 10: Umgebungstemperatur

Für die Übertragung der erfassten CPU-Temperatur und der RAM-Auslastung werden einfache, im Code <mqtt_Telemetrie_ThingSpeak_V3> leicht ersichtliche Befehle verwendet. So ist zum Beispiel folgender Code ausreichend, um die RAM-Auslastung auszulesen:

ramPercent = psutil.virtual_memory().percent

Bei der Übertragung der CPU-Temperatur musste der ausgelesene Datenstring etwas angepasst werden, damit lediglich ein Zahlenwert an ThingSpeak weitergegeben wird. Ohne diese Anpassung wäre es nicht möglich gewesen, die CPU-Temperatur auszulesen. Den Abbildungen 9 und 10 können die entsprechenden Werte für CPU und RAM entnommen werden.

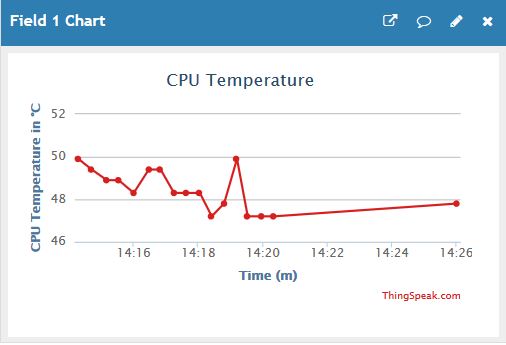
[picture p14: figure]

Abbildung 11: CPU-Temperatur

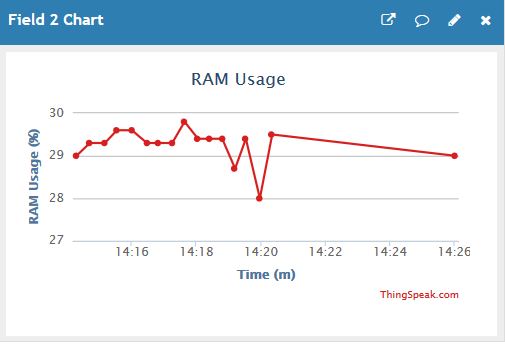
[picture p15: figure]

Abbildung 12 : Arbeitsspeicher Auslastung

Die Übergabe der Data Up- und Downloads war relativ kompliziert, da der aktuelle Wert durch einen Vergleich zwischen aktuellem Datenübertrag und vorherigen Datenübertrag ermittelt wird. Die erste Messung zeigt also zu Beginn bei beiden Feldern den Wert 0, und ab der nächsten Messung werden die aktuellen Werte angezeigt. Data Up- und Download können den Abbildungen 11 und 12 entnommen werden.

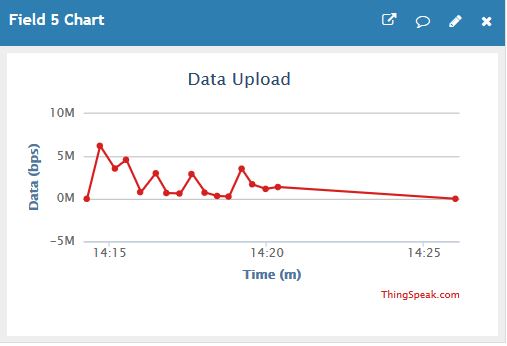
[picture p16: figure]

Abbildung 13: Data-Upload

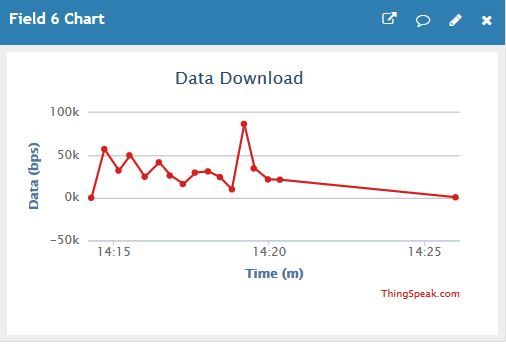
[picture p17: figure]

Abbildung 14: Data-Download

## 3.3 Twitter-Account

Das automatische Hochladen eines aufgenommenen Fotos zu einem Twitteraccount, was zuerst als optionales Ziel für das Gesamtprojekt geplant war, entwickelte sich zum Ende der Projektphase zu einem entscheidenden Bestandteil des Gesamtkonzepts der Datenübertragung. Die Anforderungen des Projekts sahen lediglich die Speicherung der entstandenen Fotos vor, welche jeweils von einem Hindernis gemacht werden sollten.

Um nun die gespeicherten Bilder automatisch an den erstellten Twitteraccount der Mohne (Mohne_2.0) zu pushen, muss über das Application Management von Twitter (apps.twitter.com) eine passende App erstellt werden. Hier hat, ähnlich wie bei ThingSpeak, die eindeutige Identifikation des Ziels für den Upload-Vorgang höchste Priorität. Über Consumer Key, Consumer Secret und Access Token, die bei erfolgreicher Einrichtung der App automatisch generiert werden, kann der Twitteraccount aus dem Python Code heraus adressiert werden.

Wenn nun der Ultraschallsensor der Hinderniserkennung ein Hindernis erkennt, wird ein Foto gemacht und automatisch zu Twitter gepusht. Das Foto kann auch manuell ausgelöst werden, allerdings nur wenn sich die Mohne im Fernsteuerungsmodus befindet. Ein weiterer Vorteil dieser Methode ist die Auslagerung der Speicherung der Fotos auf Twitter, da immer nur das aktuelle Foto gespeichert und nach erfolgtem Upload überschrieben wird.

Um das Erscheinungsbild der Tweets der Mohne etwas zu polieren, wurden noch einige Statustexte erstellt, die mit einem Hashtag versehen und mit dem entsprechenden Bild zusammen hochgeladen werden. Dabei werden die Statustexte mit der Funktion choice() zufällig ausgewählt.

Letztendlich hat sich das zuerst optionale Ziel, die Bilder automatisch zu Twitter zu pushen, als ein sehr passendes Experiment im Bereich der Datenübertragung erwiesen. Der Aufbau des Twitteraccounts ist auf Abbildung 13 gut zu sehen. Außerdem ist die Funktion aus dem Bericht angefügten Code <FernFoto.py> ersichtlich.

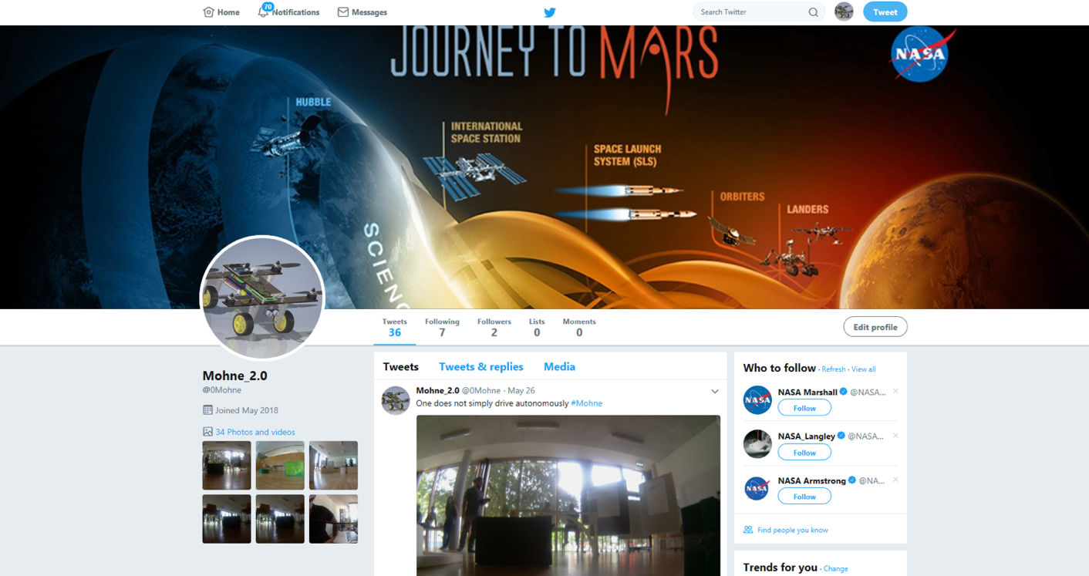
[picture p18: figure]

Abbildung 15: Mohne Twitter-Account

(https://twitter.com/0mohne?lang=de)

# 4. Hindernis-Parcours

## 4.1 Karte mit Fahrstrecke

Das Team-Mohne bekam die Fahrstrecke D (siehe Abbildung 14) zugewiesen. Diese Strecke musste im ferngesteuerten Modus abgefahren werden. Hierbei muss jeder Punkt bzw. jedes Quadrat angefahren und durchfahren werden.

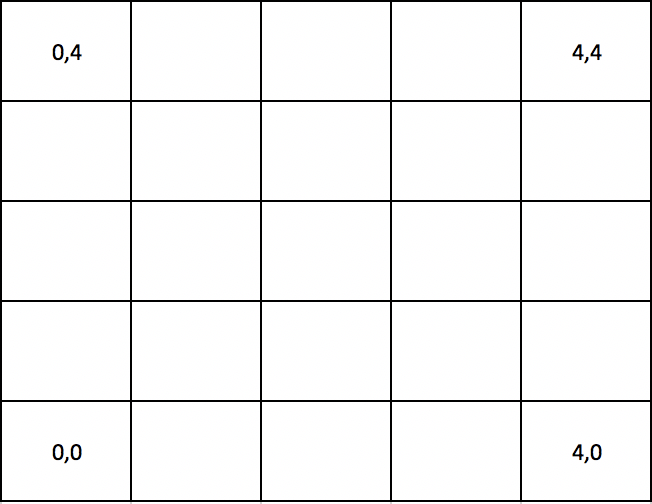
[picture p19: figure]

Abbildung 16: Strecke D

Für das autonome Fahren wurden Hindernisse auf derselben Karte ohne System verteilt und die Mohne musste das Ziel (4,4) erreichen. Wie die das autonome Fahren funktioniert hat, ist aus dem Code zu entnehmen
(https://github.com/gchrizZz/Mohne/tree/master/02_Quellcode).

# 5. Es wird doch alles anders als geplant

Die Generalprobe unseres Marsrovers ging leider gehörig schief. Während einem der letzten Tests ist einer der vier ESC (Electronic Speed Control) kaputt gegangen. Da die Mohne nur mit allen vier ESC fliegen kann, musste hier eine schnelle und unkomplizierte Lösung gefunden werden. Hierzu wurde die physikalische Grundlage des Arudino-Fahrezeuges gewählt. Nun wurde das Design und die notwendigen Komponenten auf das neue Grundgerüst umgebaut und durch entsprechende Überstunden (Nachtschicht) ist es dem Team-Mohne gelungen, ein fahrtüchtiges und einsatzfähiges Fahrzeug zu bauen. Mit diesem neu gestaltenen Fahrezeug wurde in den Wettbewerb gestartet und die Anforderungen umgesetzt.

Alle Programme, Zeichnungen und Konzeptentwicklungen liegen unter folgendem Link bereit:

https://github.com/gchrizZz/Mohne

[^1] Vgl. (Hewlett Packard Enterprise Development LP, 2018)

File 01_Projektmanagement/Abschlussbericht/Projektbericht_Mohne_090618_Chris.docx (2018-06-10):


Project Data Explorer - Mohne

Projektbericht

Entwicklung eines Fahrzeugs für autonome/ ferngesteuerte Datenerfassung inklusive der Umweltbedingungen

Eingereicht bei:

Fachhochschule Kufstein Tirol Bildungs GmbH

Studiengang Smart Products & Solutions

Verfasser:

Anna Duregger, Christian Gruber, Christoph Jungwirth, Maximillian Möbes, Ludwig Paula, Markus Wiesmüller

Abgabedatum:

10.06.2017

# List of Figures

# List of Tables

Es konnten keine Einträge für ein Abbildungsverzeichnis gefunden werden.

# List of Abbreviation

# Kurzfassung

# Abstract

# 1. Conecpt Development

Aufgrund der im letzten Semester geschaffenen Basis wurde die „Mohne“ weiterentwickelt. Alternativ gab es noch die Idee ein einfaches Auto zu konstruieren um damit die Anforderungen zu erfüllen. Letztendlich wurde die Entscheidung zugunsten der bereits gebauten Drohen getroffen und wir auf dieser Basis weiterentwickeln werden.

Für das neue Projekt wurden die folgenden Kriterien des Lektoren Teams gestellt:

- Eigenschaften des Fahrzeuges: Fahrmodus, Telemetrie Daten erfassen und übertragen
- Datenerfassung: Umweltbedingungen permanent erfassen
- Digitaler Zwilling in MATLAB: Fahrzeug (mechanisches Modell-Kräfte)
- Simulation: Raspberry Pi und Arduino Simulator
- Tracks: ferngesteuert und autonom

Die obenstehenden Punkte werden im nachfolgenden Bericht detailliert erläutert und darauf eingegangen.

## 1.1 Konzept der Fahrmodi

Die beiden Konzepte der Fahrmodi bestehen aus den Modi autonom Fahren und ferngesteuertes Fahren.

Bei der Aufgabenstellung autonomes Fahren – Obstacle Detection - sind die Anforderungen folgende:

- Eindeutige markierte Hindernisse müssen umfahren werden
- Die Hindernisse müssen abfotografiert werden
- Es werden keine Begrenzungswände verwenden
- Startpunkt lieg bei (0,0)
- Endpunkt wird vorgegeben
- Erfassen der Daten der verbauten Sensoren via ThingsSpeak und MathLab

Beim ferngesteuerten Fahren - Datenerfassung sind folgende Anforderungen:

- Startpunkt bei (0,0)
- Abfolge von Messfeldern wird je Team vorgegeben
- Hindernisse müssen umfahren werden
- Explorer wird ferngesteuert (Eingabegerät offen; Eingabe von Koordinaten, Steuerbefehle mittels Joystick)
- Erfassen der Daten der verbauten Sensoren via ThingsSpeak und MathLab

### 1.1.1 autonom

Um den Parcours autonom zu absolvieren wurden zusätzliche Sensoren verwendet, mit denen diese Aufgabe vereinfacht wird. Zum einen wurde ein Gyroskop angeschlossen um die Orientierung im Raum zu vereinfachen. Zum anderen ein Ultraschallsensor damit Hindernisse erkannt werden können.

Für die Programmierung wurde der Raspberry Pi und der Arduino verwendet. Auf dem Arduino ist die Motorsteuerung gespeichert und auf dem Pi die Kamerafunktion und der Array. Beide Computer kommunizieren mithilfe einer i2c-Verbindung und senden Zahlen hin und her, welche die verschiedene Funktionen auslösen. Das autonome Fahren beim Auto konnte leider nicht komplett absolviert werden, da das Auto selber nicht in einer Linie fährt, sondern eine Rechtsneigung besaß. Es fuhr so lange vorwärts, bis sich ein Hindernis 30 Zentimeter vor dem Fahrzeug befindet. Dieser Wert wird mit einem Ultraschallsensor berechnet. Dieser ist am Arduino angeschlossen und muss dem Raspberry Pi mitteilen, dass ein Hindernis vorhanden ist und ein Foto gemacht werden muss. Durch die i2c-Verbindung wird vom Arduino die Zahl 7 versendet. Das Problem hierbei ist, dass der Arduino nicht von sich aus Zahlen senden kann. Somit muss der Raspberry Pi regelmäßig den Arduino fragen, ob ein Hindernis vorhanden ist. Diese Frage wird mithilfe einer Zahl jede Sekunde gestellt und geantwortet wird mit einen von zwei Zahlen. Entweder ist ein Hindernis vorhanden oder die Bahn ist frei. Nachdem der Raspberry Pi die Antwort erhalten hat, wird entsprechend gehandelt. Bei einem Objekt wird die Kamerafunktion ausgelöst und das Bild wird auf Twitter geladen. Nachdem das Foto geschossen wurde, wird eine Rechtskurve gefahren und dann fährt das Auto weiter.

Die Motorsteuerung wurde aus dem Ersten Projekt im 1. Semester übernommen und angepasst. Um Platz auf dem Breadboard und Pins auf dem Arduino zu sparen wurde nur eine H-Brücke gebaut und die linken bzw. rechten Reifen parallelgeschaltet. Da die Motoren sehr schwach sind, wurde immer der höchste Wert von 255 verwendet. Bei den Links- und Rechtsdrehungen wird wie ein Panzer gefahren. Das heißt, dass beide Seiten gegenfahren bis sich das Auto in einem Winkel von 90 Grad gedreht hat.

### 1.1.2 ferngesteuert

Bei der Aufgabe das Fahrzeug über den Parcour per Fernsteuerung zu fahren gibt es viele Möglichkeiten die Fernsteuerung zu kreieren. Wir haben uns dann schlussendlich für die Laptoptastatur entschieden. Dies hat den Vorteil, dass jeder den Code testen kann ohne eine physische Fernsteuerung mitnehmen zu müssen und falls es Probleme bei der Verbindung gibt kann die Mohne per Not-Stopp ausgeschaltet werden. Da das Fahrzeug bereits mit einem Samba Server verbunden ist war die Remote-Steuerung leicht zu verwenden und in der Testphase konnten die verschiedenen Programme schnell verändert werden. Der Code für die Fernsteuerung heißt ‚FernFoto.py‘ und kommt von ‚Fernsteuerung‘ und ‚Foto‘.

Die Motorsteuerung war auf dem Arduino gespeichert. Dies war bei der ursprünglichen Mohne, wie auch bei unserem endgültigen Auto der Fall. Auf die Motorsteuerung selber wurde bereits im Abschnitt Autonom eingegangen.

Der Code für die Fernbedienung wurde auf dem Raspberry Pi mithilfe eines Keyloggers geschrieben. Der verwendete Logger kommt aus die pynput Library. Dies hatte den Vorteil, dass es auch eine Key Release Funktion gab und dadurch die Mohne stoppt, wenn eine Taste losgelassen wurde. Der Nachteil war allerdings, dass der Keyloggers nicht zusammen mit Schleifen funktioniert. Somit konnte der Raspberry Pi nicht selbständig Fotos schießen. Dieses Problem wurde gelöst indem ein separater Tastendruck die Kamera auslöst und das Bild auf Twitter ho geladen wird.

Die Mohne wird klassisch mit den Pfeiltasten gesteuert. Beim Drücken der Leertaste entsteht das Foto und mit der Escape-Taste wird das Programm gestoppt. Wenn keine Taste gedrückt wird oder eine losgelassen wird werden die Motoren ausgeschaltet.

Jetzt müssen die Befehle nur noch an den Arduino geschickt wird, damit diese umgesetzt werden. Die im Unterricht gelernte i2c-Verbindung wurde verwendet und modifiziert. Jede Taste wurde einer Zahl zugeordnet, die an den Arduino geschickt wird. Wenn die Motoren stoppen sollen wird auch eine Zahl gesendet.

Der Code auf dem Arduino heißt ‚Fern_1.0‘. Auf diesem wurden bereits Klassen für die jeweiligen Richtungen geschrieben. Also vorwärts, rückwärts, rechts und links. Dazu natürlich noch die Stopp Funktion. Durch die i2c-Verbindung wartet der Arduino auf die Zahlen, welche vom Raspberry Pi gesendet werden. Bei der Zahl 1 wird nach vorne gefahren. Bei der 2 nach rechts. Wird die 3 gesendet nach Links und bei der 4 rückwärts. Die Nummer 5 wird für die Stopp Funktion verwendet.

Die Fernsteuerung lief trotz vielen Schnittstellen sehr präzise und ohne Verzögerung.

## 1.2 Fahrzeugaufbau

### 1.2.1 CAD als Unterstützung für die Fertigung und Designentwicklung

Die Mohne besteht aus 66 Einzelteilen, Kabel, Schrauben, Muttern und Kabelbinder sind hierbei nicht berücksichtigt.

In Abbildung 1 ist das fertige CAD Modell als Explosionsdarstellung aufgezeigt, um die Komplexität des Modells zu veranschaulichen.

Ohne ein ausgereiftes CAD-Modell ist eine ordnungsgemäße Fertigung der Mohne nicht möglich. Außerdem hilft das digitale Modelle etwaige Lücken bzw. Versäumnisse in der Konzeption aufzudecken, noch bevor eine zeitintensive Fertigung gestartet wird.


Abbildung 1: Explosionsdarstellung Mohne


Abbildung 2: Rendering Ansicht Mohne

Abbildung 2 zeigt ein Rendering Bild der auskonstruierten Mohne. Im Zuge der Designentwicklung wurden folgende vier Designschwerpunkte hinsichtlich der NASA als Kunde getroffen:

1. Entwicklung eines individuellen und additiv gefertigten Gehäuses zum Schutz der Steuergeräte
2. Modulares Sensorplattenkonzept, welches einen Wechsel durch reine Schraub und Steckverbindungen ermöglicht
3. Einsatz von Kohlefaser als modernes, vielseitiges und gewichtsoptimiertes Material
4. Solarmodule zum Laden des Akkumulators

Das gesamte CAD Modell und das Designkonzept kann unter https://github.com/gchrizZz/Mohne abgerufen werden.

### 1.2.2 Elektronik

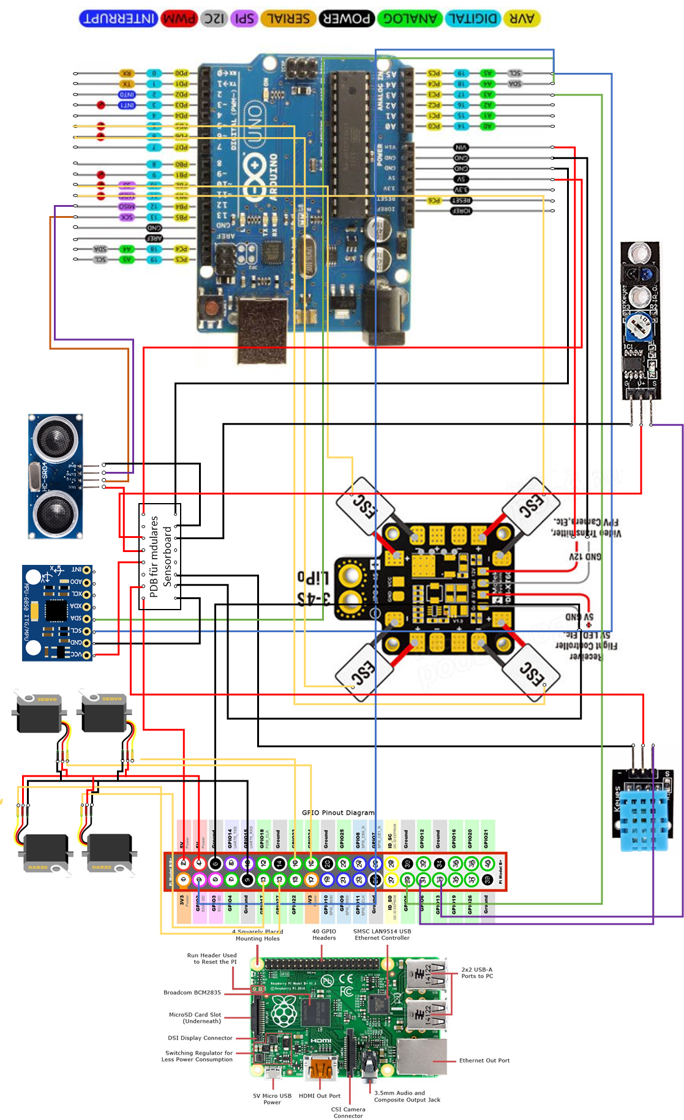
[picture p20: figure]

Abbildung 3: Elektronische Komponenten und Verkabelung Mohne

Abbildung 3 zeigt den Kabelbaum und die elektrischen Komponenten der Mohne auf. Dieser Plan berücksichtigt lediglich die geforderten Sensoren, dennoch ist die Designentscheidung einer modularen Sensorplatte bereits berücksichtigt. Hierfür wurde ein gesondertes PDB ausschließlich für die Stromversorgung aller angebrachter Sensoren eingearbeitet. Somit müssen zusätzliche Sensoren lediglich an diesem PDB und mit Ihren Signalkabeln an das vorgesehene Steuergerät (Pi oder Uno) angeschlossen werden. Löten ist nicht mehr notwendig.

### 1.2.3 Kommunikation

Der Zugriff der Mohne wird nach wie vor über einen Samba Server realisiert. Samba ist ein freies Programmpaket, das es ermöglicht Windows-Funktionen wie die Datei und Druckdienste unter anderen Betriebssystemen zu nutzen und die Rolle eines Domain Controllers anzunehmen. Es implementiert hierfür unter anderem das Server Message Block/Common Internet File System-Protokoll (SMB/CIFS-Protokoll). Im Projekt wurde Samba als DC und DNS verwendet, damit man via RDP über WLAN auf den Pi zugreifen kann, ohne eine statische IP im Pi hinterlegen zu müssen. Der hostname der Drohne lautet „Mohne“.

Die Kommunikation zwischen dem MPU, dem Arduino Uno und dem Pi wurde via I²C realisiert. I²C (gesprochen "I quadrat C") ist ein synchroner serieller Zweidraht-Bus, der jeweils eine bidirektionale Daten- und Taktleitung verwendet und für die Kommunikation zwischen ICs über kleine Distanzen geeignet ist. Die Bezeichnung steht für IIC, Inter-Integrated Circuit.

Der Kombi-Sensor (KY-015), als auch der Linetracking Sensor (KY-033) sind mittels jeweils eines GPIO Pins mit dem Pi verbunden. Somit können die Daten von diesen direkt über das digitale Eingangssignal am Pi verarbeitet werden.

Da die Logikverarbeitung für die das autonome Fahren hinsichtlich Linetracking und Orientierung in einem Schachbrett-Array auf dem Pi abläuft, kann man mit dieser einfachen und direkten Kommunikation, die Logik am leichtesten realisieren.

Die Servos, welche für die Ausrichtung der Motorhalterung an allen vier Armen der Drohne verantwortlich sind, werden ebenfalls via GPIO Pins an den Pi angebunden. Jedoch wird diesen ein imitiertes PWM Signal gesendet, um sie zu steuern.

Der Ultraschallsensor (USS) ist mittels zwei IO Pins, direkt am Arduino angeschlossen. Auf diesem Weg kann die unmittelbare Hinderniserkennung am schnellsten realisiert werden. Da der USS ausschließlich mit dem Arduino Uno kommuniziert, muss die Logikverarbeitung hierfür im C++ Code auf dem Arduino stattfinden.

# 2. Model Based Analytics

Der Grundgedanke von Model Based Analytics ist die virtuelle bzw. digitale Darstellung eines physischen Modells. Dieses Modell wird in der digitalen Welt analysiert und interpretiert. Dies ist eine Methode gewisse Problemstellungen virtuell darzustellen und diese als Simulation zu verwenden.

Für unser Projekt wurde der Digitale Zwilling gewählt um diese Problemstellung darzustellen und eine entsprechende Lösung zu finden.

## 2.1 Digitaler Zwilling

Das Konzept eines digitalen Zwillings besteht aus drei Elementen: einem physischen Zwilling in der realen Welt, einem digitalen Zwilling im virtuellen Raum, der sowohl alle alten betrieblichen Daten als auch die Echtzeitdaten des physischen Zwillings abbildet, und die Interkonnektivität, die es den Zwillingen ermöglicht, die Informationen auszutauschen. Digitale Zwillingen können für Simulationen verwendet werden und für Einblicke in den arbeitenden Zwilling, um Prozesse zu überwachen und mögliche Fehler zu entdecken.[^1]

Im folgenden Abschnitt werden nähere Beschreibungen zum digitalen Zwilling angeführt.

### 2.1.1 Allgemein

Ein digitaler Zwilling ist eine virtuelle Modellbildung zum Beispiel eines Prozesses, eines Produkts oder einer Dienstleistung, welches die reale und virtuelle Welt verbindet. Digitale Zwillinge verwenden reale Daten von installierten Sensoren, welche die Arbeitsbedingungen oder Position von Maschinen repräsentieren. Diese Kopplung der virtuellen und realen Welten ermöglicht die Analyse von Daten und die Überwachung von Systemen, um Probleme verstehen und bearbeiten zu können, bevor sie überhaupt auftreten. Ausfallzeiten können frühzeitig vermieden werden und dadurch neue Chancen entwickeln und mithilfe von Computersimulationen, damit die Zukunft besser geplant werden kann. Heutzutage werden digitale Zwillinge eine geschäftliche Notwendigkeit, weil der gesamte Lebenszyklus eines Produkts, Prozesses oder Geschäftsmodells abdeckt werden kann und somit die Grundlage für verbundene Produkte und Dienstleistungen bilden.

Für den sogenannten digitalen Zwilling sind folgende Anforderungen notwendig: das abzubildende reale Objekt, den digitalen Zwilling im virtuellen Raum und Informationen, welche die beiden miteinander verbinden. Digitale Zwillinge können dadurch die operative und auch finanzielle Leistungsfähigkeit eines Objekts wie einer Anlage oder einer Dienstleistung verbessern und in Echtzeit dargestellt werden.

In der ersten Phase „Design“ geht es um den Umgang mit komplexen Produktanforderungen, schnellen Entwicklungszyklen und strengen regulatorischen Anforderungen. In der zweiten Phase „Erstellung (manufacturing)“ kann der Zwilling helfen, bessere Effizienz, Qualität und höheren Ertrag in der Erstellung zu erreichen. In der dritten Phase „Nutzung (operate)" kann ein digitaler Zwilling u. A. eingesetzt werden, um die Verfügbarkeit von Objekten (z. B. Maschinen) zu verbessern. In der vierten Phase „Wiederverwertung (Recycling)“ kann der ein digitaler Zwilling z.B. für die Ersatzplanung oder der Eruierung von Upcycling-Potenzialen eingesetzt werden.

### 2.1.2 Projektbezogen

Unser PlanB des Projektes Data Explorer wurde am Tag zu einem Auto umgebaut und deren Funktionen erweitert bzw. ergänzt. Am Auto herrscht ein mechanisches Kräftemodell, welches im folgenden Kapitel dargestellt wird. Dadurch haben wir entschieden, dass wir die Kraft des Motors mit der Beschleunigung als Digitalen Zwilling modellieren bzw. darstellen wollen. Interessant an der Darstellung wird, wie sich die Beschleunigung „a“ während der Datenerfassung verhält. Die Erfassung der Daten erfolgt mithilfe der Matlab Software und dessen Mobile App. Durch die Kommunikation zwischen den beiden Anwendungen kann eine Erfassung der Daten mit verschiedenen Sensoren wie Beschleunigungssensor erfasst werden. Es kann analysiert werden, ob bei der Absolvierung des vorgegebenen Parcours eine Verminderung der Beschleunigung eintritt, wenn ein Hindernis kommt oder eine Kurve nach links oder rechts gemacht wird. Der digitale Zwilling wird in einem Plot der Matlab Software dargestellt, damit das Diagramm entsprechend erläutert und interpretiert werden kann.

### 2.1.3 Material und Methoden

Für die Erfassung des digitalen Zwillings unseres Sommerprojektes haben wir uns entschieden, dass wir die Anwendung der Matlab App verwenden werden, da wir kein Logfile über den Raspberry Pi erstellen. Für die Anwendung ist die Matlab Software und der Download der dazugehörigen Matlab Mobile App notwendig. Zu Beginn wird die Matlab Mobile App am Smartphone installiert, egal ob Android oder iOS Betriebssystem. Am Smartphone können die unterschiedlichsten Sensoren wie Beschleunigungs-, Magnetfeld-, Positions-, Winkelgeschwindigkeits- und Orientierungssensor aktiviert werden. In der Software ist eine Installation eines Add-Ons zu erledigen. Um eine Verbindung zwischen der Software und der App herzustellen, wird in der Kommandozeile der Software der Konnektor aktiviert. Es wird nun die funktionierende IP-Adresse angezeigt, welche im Smartphone eingegeben wird, um eine Kommunikation herstellen zu können. Als nächsten Schritt wird der Link von PC und Smartphone erzeugt und es können sowohl am Smartphone und in der Kommandozeile durch bestimmte Matlabbefehle die Sensoren aktiviert werden. Für eine korrekte Datenerfassung werden durch Befehle in der Kommandozeile die Datenaufnahme der Messwerte aktiviert und auch wieder beendet. Mit den erfassten Sensordaten des Smartphones können die Daten auf verschiedensten Arten analysiert und auch dargestellt werden. Die Daten können in einem Diagramm inklusiver Legende in Matlab dargestellt werden.

### 2.1.4 Mechanisches Modell des Fahrzeuges

Im folgenden Bild wird das mechanische Modell unseres Fahrzeuges abgebildet. Das Kräftemodell des Fahrzeuges besteht aus der Reibungskraft, die Erdanziehungskraft, die Kraft des Motors in der Vorwärtsbewegung und die Kraft des Autos.


Abbildung 4: Mechanisches Kräftemodell des Autos

### 2.1.5 Ergebnisse

Aus der Datenerfassung der Matlab App konnte die Kraft des Motors erfasst und gemessen werden. Die Daten wurden während unseres autonomen Fahrens, welches leider in der kurzen Zeit nicht möglich war fertig zu programmieren, aufgenommen. Anhand der Daten, die auf die Software von Matlab übertragen wurden kann herausgelesen werden, dass unser Programm eine relativ kontinuierliche Geschwindigkeit durchfährt. Daraus resultiert sich, dass unser Fahrzeug, wegen den nicht fertigen ferngesteuertem Programm, nicht immer Objekte bzw. Hindernisse erkennen kann und somit sich nicht mit einer kontinuierlichen Geschwindigkeit fortbewegt.

Mit der Darstellung der Beschleunigung ist keine kontinuierliche Beschleunigung ersichtlich. Der programmierte Code enthält leider keine konkrete Struktur bzw. Abfolge und somit resultiert sich ein relativ hektisches Beschleunigungsdiagramm. In der Mitte des Diagramms kann man erkennen, dass das Fahrzeug einen Stillstand hat und womöglich ein Hindernis erkennen konnte.

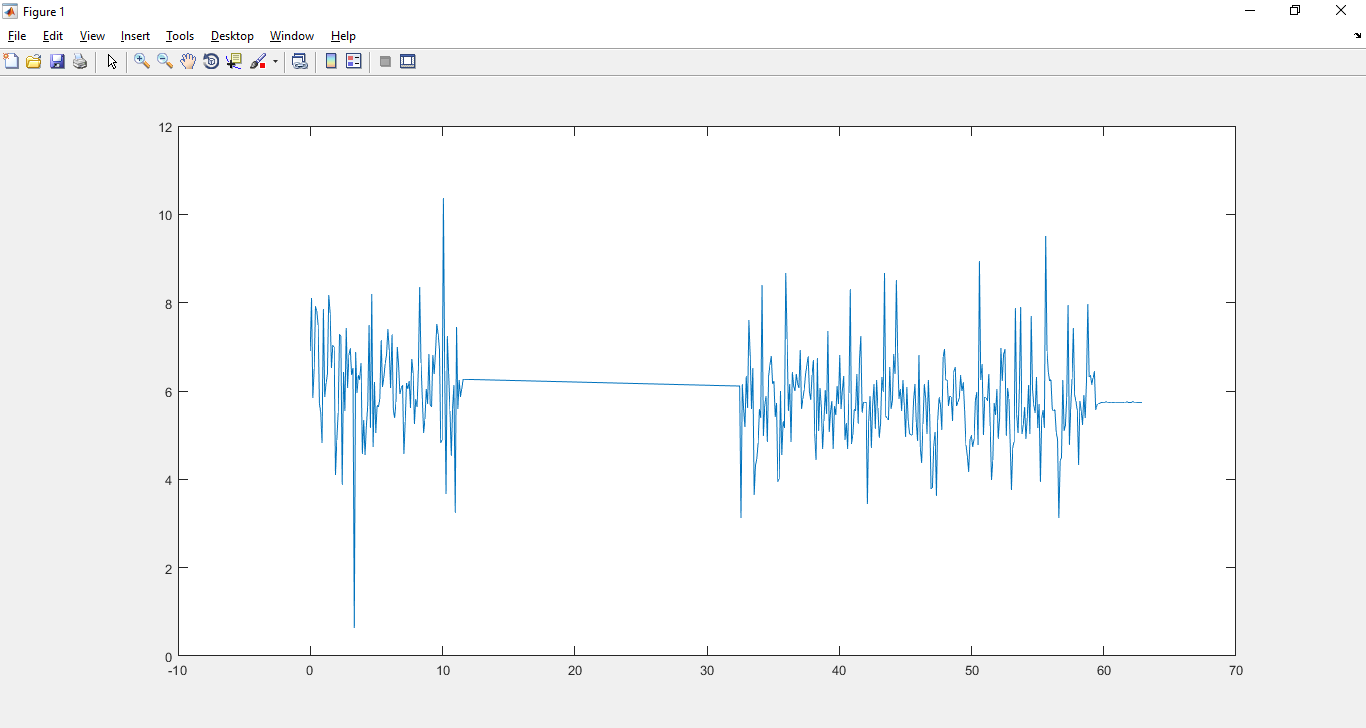
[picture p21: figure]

Abbildung 5: Diagramm für die Beschleunigung

Im folgenden Plot von Matlab ist die Winkelgeschwindigkeit dargestellt. Auf dieser Darstellung erkennt man wie sich das Fahrzeug in den Richtungen verändert. Wie schon vorher erläutert haben wir den Fernsteuerungsmodus leider nicht bis zum Ende programmieren können. Im Diagramm ist schön zu sehen, wie oft und schnell das Fahrzeug die Richtung ändert. Das ist der Grund, dass das Programm nicht in der Zeit fertig geworden ist. Deswegen fährt das Fahrzeug willkürlich durch den Raum und in der Gerade des Diagramm hat es an gehalten, weil es womöglich ein Hindernis erkannt hat. Ursprünglich ist es gedacht, dass das Fahrzeug einem Hindernis ausweicht, jedoch nach dem Diagramm sind auf unserem vorgegebenen Parcour sehr viele Hindernisse platziert worden.

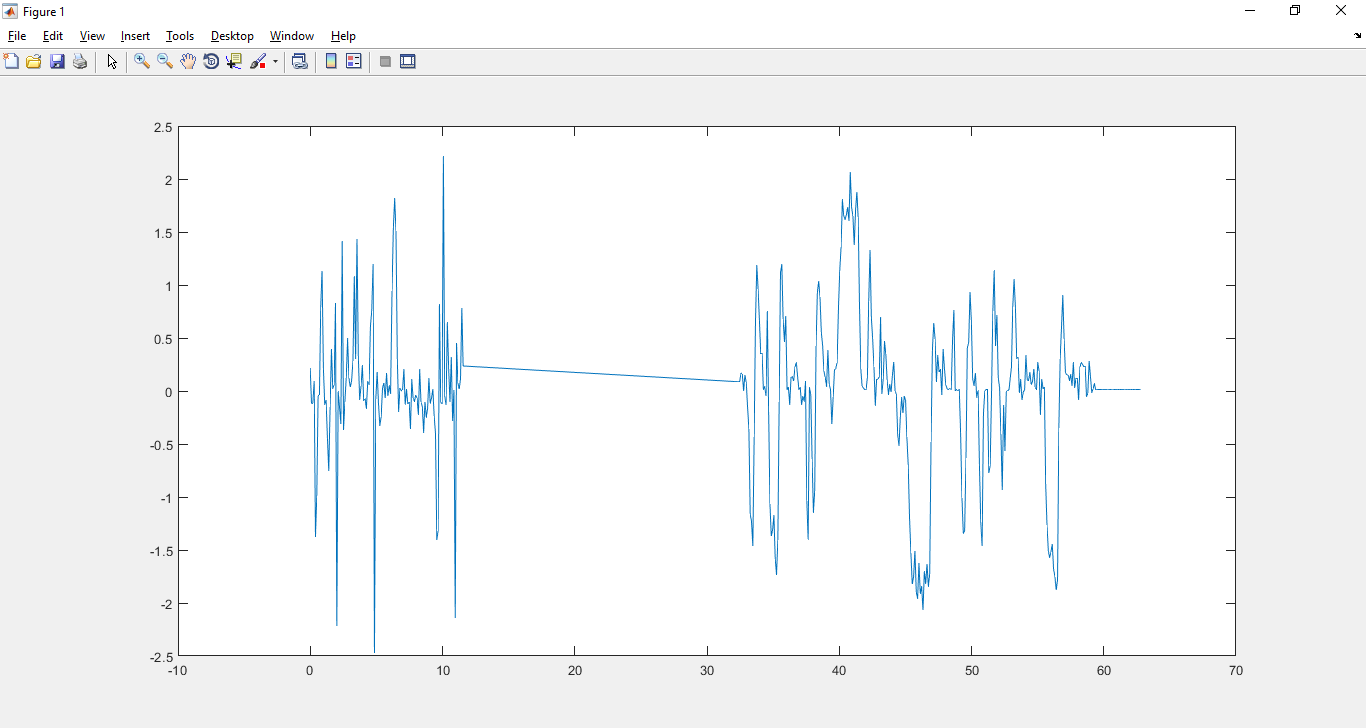
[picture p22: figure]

Abbildung 6: Diagramm für die Winkelgeschwindigkeit

### 2.1.6 Konklusion

Am Beispiel der beiden Diagramme kann man erkennen, dass unser programmierter Quellcode leider nicht dem Fernsteuerungsmodus entspricht. Das Fahrzeug kann durch die Bilderkennung nicht kontinuierlich die Hindernisse erkennen und daraufhin die Geschwindigkeit reduzieren bzw. nach dem Stillstand wieder beschleunigen. In der Mitte des Diagramms ist ein Stillstand zu erkennen, weil hier womöglich ein Hindernis erkannt wurde. In beiden Abbildungen ist die Beschleunigung sowohl die Winkelgeschwindigkeit sehr hektisch, da das Programm aus zeitlichen Gründen nicht fertig geschrieben werden konnte.

# 3. Simulation

## 3.1 Pi Simulation

## 3.2 Arduino Simulation

# 4. Datenübertragung

## 4.1 Thinkspeak

Der zentrale Teil der Anforderungen für das Projekt war die Übertragung von Messdaten der Fahrzeuge über das Web hin zu einer Cloudplattform, hier ThingSpeak. ThingSpeak ist eine Open IoT Platform (Cloudservice), die im Zusammenspiel mit MATLAB eine Menge Funktionen bietet, darunter auch die Übertragung von Messdaten. Dabei waren gewisse Parameter vorgegeben, andere wiederum waren, in einem bestimmten Rahmen, frei wählbar. Für die Übertragung der Daten kam sowohl das HTTP/REST-Protokoll als auch das MQTT-Protokoll in Frage. Die Entscheidung fiel zugunsten des MQTT-Protokolls, das speziell für embedded devices mit geringer RAM- und CPU-Leistung. Darüber hinaus verbraucht MQTT sehr viel weniger Bandbreite und eignet sich daher optimal für die Verwendung mit Arduino und Raspberry Pi. Zusätzlich gibt es die Möglichkeit, Nachrichten mit unsecured TCP zu senden, womit nochmal die Performance verbessert wird.

Um das Protokoll für die Übertragung der Messdaten zu nutzen, ist es erforderlich, eine entsprechende Library auf dem Raspberry Pi zu installieren, in diesem Fall die Paho Library.

In dem dazugehörigen Code <mqtt_Telemetrie_ThingSpeak_V3> sind einige Funktionen derzeit auf „False“ gesetzt, da sie einerseits die Übertragung der entsprechenden Nachricht auf anderen Wegen ermöglichen (statt UnsecuredTCP zum Beispiel UnsecuredWebsockets) oder das Ansprechen eines zweiten Channels auf ThingSpeak ermöglichen. Die Verbindung zu ThingSpeak ließ sich im Nachhinein relativ einrichten, vor allem da es auch in einer Übungsveranstaltung im Studienfach Datenübertragung vorgestellt wurde. Das eigentliche Übertragen der Telemetriedaten wird unter Punkt X.X näher beschrieben.

## 4.2 Auswertung

Nach erfolgreichem Herstellen einer Verbindung zu ThingSpeak sollten nun die geforderten Daten aufgenommen und automatisch an ThingSpeak übertragen werden. Die CPU-Temperatur, RAM-Auslastung, Data Up- und Download werden vom Raspberry Pi selbst erfasst, im Gegensatz zu Luftfeuchtigkeit und Umgebungstemperatur, die über einen Kombisensor (KY-015) ausgelesen werden.

Für diesen Kombisensor muss eine spezielle Library von Adafruit installiert werden, Adafruit_DHT. Nach der Installation kann der Sensor ausgelesen werden, indem man einen entsprechenden GPIO-Pin definiert. Der Kombisensor gibt dann zuerst den Wert für die Luftfeuchte und dann den Wert für die Umgebungstemperatur aus. Die erfassten Werte für Luftfeuchte und Umgebungstemperatur können den Abbildungen 6 und 7 entnommen werden.


Abbildung 6: Luftfeuchtigkeit


Abbildung 7: Umgebungstemperatur

Für die Übertragung der erfassten CPU-Temperatur und der RAM-Auslastung werden einfache, im Code <mqtt_Telemetrie_ThingSpeak_V3> leicht ersichtliche Befehle verwendet. So ist zum Beispiel folgender Code ausreichend, um die RAM-Auslastung auszulesen:

ramPercent = psutil.virtual_memory().percent

Bei der Übertragung der CPU-Temperatur musste der ausgelesene Datenstring etwas angepasst werden, damit lediglich ein Zahlenwert an ThingSpeak weitergegeben wird. Ohne diese Anpassung wäre es nicht möglich gewesen, die CPU-Temperatur auszulesen. Den Abbildungen 8 und 9 können die entsprechenden Werte für CPU und RAM entnommen werden.


Abbildung 8: CPU-Temperatur


Abbildung 9: Arbeitsspeicher Auslastung

Die Übergabe der Data Up- und Downloads war relativ kompliziert, da der aktuelle Wert durch einen Vergleich zwischen aktuellem Datenübertrag und vorherigen Datenübertrag ermittelt wird. Die erste Messung zeigt also zu Beginn bei beiden Feldern den Wert 0, und ab der nächsten Messung werden die aktuellen Werte angezeigt. Data Up- und Download können den Abbildungen 10 und 11 entnommen werden.


Abbildung 10: Data-Upload


Abbildung 11: Data-Download

## 4.3 Twitter-Account

Das automatische Hochladen eines aufgenommenen Fotos zu einem Twitteraccount, was zuerst als optionales Ziel für das Gesamtprojekt geplant war, entwickelte sich zum Ende der Projektphase zu einem entscheidenden Bestandteil des Gesamtkonzepts der Datenübertragung. Die Anforderungen des Projekts sahen lediglich die Speicherung der entstandenen Fotos vor, welche jeweils von einem Hindernis gemacht werden sollten.

Um nun die gespeicherten Bilder automatisch an den erstellten Twitteraccount der Mohne (Mohne_2.0) zu pushen, muss über das Application Management von Twitter (apps.twitter.com) eine passende App erstellt werden. Hier hat, ähnlich wie bei ThingSpeak, die eindeutige Identifikation des Ziels für den Upload-Vorgang höchste Priorität. Über Consumer Key, Consumer Secret und Access Token, die bei erfolgreicher Einrichtung der App automatisch generiert werden, kann der Twitteraccount aus dem Python Code heraus adressiert werden.

Wenn nun der Ultraschallsensor der Hinderniserkennung ein Hindernis erkennt, wird ein Foto gemacht und automatisch zu Twitter gepusht. Das Foto kann auch manuell ausgelöst werden, allerdings nur wenn sich die Mohne im Fernsteuerungsmodus befindet. Ein weiterer Vorteil dieser Methode ist die Auslagerung der Speicherung der Fotos auf Twitter, da immer nur das aktuelle Foto gespeichert und nach erfolgtem Upload überschrieben wird.

Um das Erscheinungsbild der Tweets der Mohne etwas zu polieren, wurden noch einige Statustexte erstellt, die mit einem Hashtag versehen und mit dem entsprechenden Bild zusammen hochgeladen werden. Dabei werden die Statustexte mit der Funktion choice() zufällig ausgewählt.

Letztendlich hat sich das zuerst optionale Ziel, die Bilder automatisch zu Twitter zu pushen, als ein sehr passendes Experiment im Bereich der Datenübertragung erwiesen. Der Aufbau des Twitteraccounts ist auf Abbildung 12 gut zu sehen. Außerdem ist die Funktion aus dem Bericht angefügten Code <FernFoto.py> ersichtlich.


Abbildung 12 (https://twitter.com/0mohne?lang=de)

# 5. Hindernis-Pacour

## 5.1 Karte mit Fahrstrecke

Das Team-Mohne bekam die Fahrstrecke D zugewiesen. Diese Strecke musste im ferngesteuerten Modus abgefahren werden. Hierbei muss jeder Punkt bzw. jedes Quadrat angefahren und durchfahren werden.


Abbildung 13: Strecke D

Für das autonome Fahren wurden Hindernisse auf derselben Karte ohne System verteilt und die Mohne musste das Ziel (4,4) erreichen. Wie die das autonome Fahren funktioniert hat, ist aus dem Code zu entnehmen
(https://github.com/gchrizZz/Mohne/tree/master/02_Quellcode).

## 5.2 Karte mit Messpunkte

## 5.3 Fahrstrecke mit Messungen

# 6. Es wird doch alles anders als geplant

Die Generalprobe unseres Marsrovers ging leider gehörig schief. Während einem der letzten Tests ist einer der vier ESC (Electrronic Speed Control) kaputt gegangen. Da die Mohne nur mit allen vier ESC fliegen kann, musste hier eine schnelle und unkomplizierte Lösung gefunden werden. Hierzu wurde die physikalische Grundlage des Arudino-Fahrezeuges gewählt. Nun wurde das Design und die notwendigen Komponenten auf das neue Grundgerüste umgebaut und die entsprechenden Programme und Codes an die neuen gegebenheiten angepasst. Innerhalb weniger Stunden ist es dem Team-Mohne gelungen ein fahrtüchtiges und einsatzfähiges Fahrezeug zu bauen. Mit diesem neu gestaltenen Fahrezeug wurde in den Wettbewerb gestartet und die Anforderungen umgesetzt.

# 7. Zusammenfassung

[^1] Vgl. (Hewlett Packard Enterprise Development LP, 2018)

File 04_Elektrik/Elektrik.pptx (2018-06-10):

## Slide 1

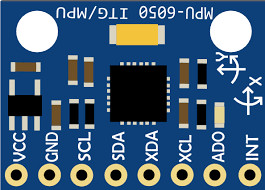
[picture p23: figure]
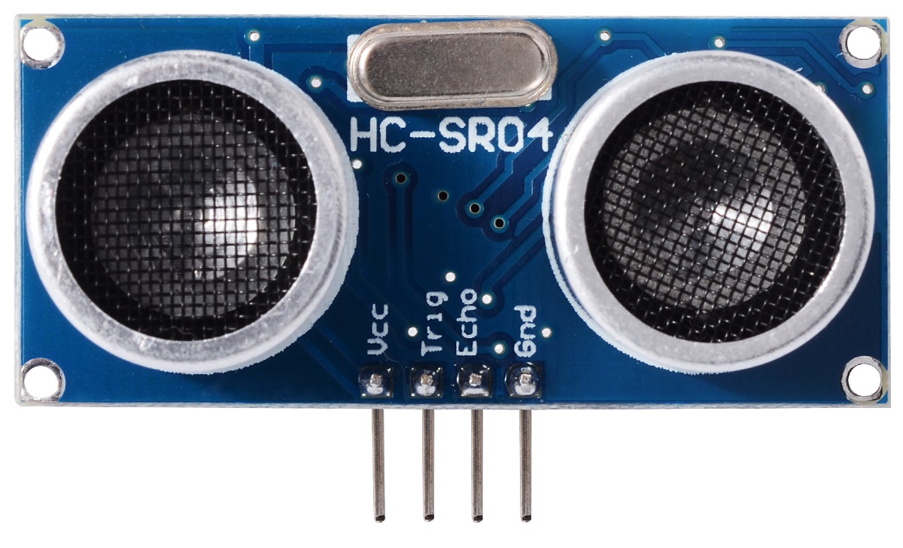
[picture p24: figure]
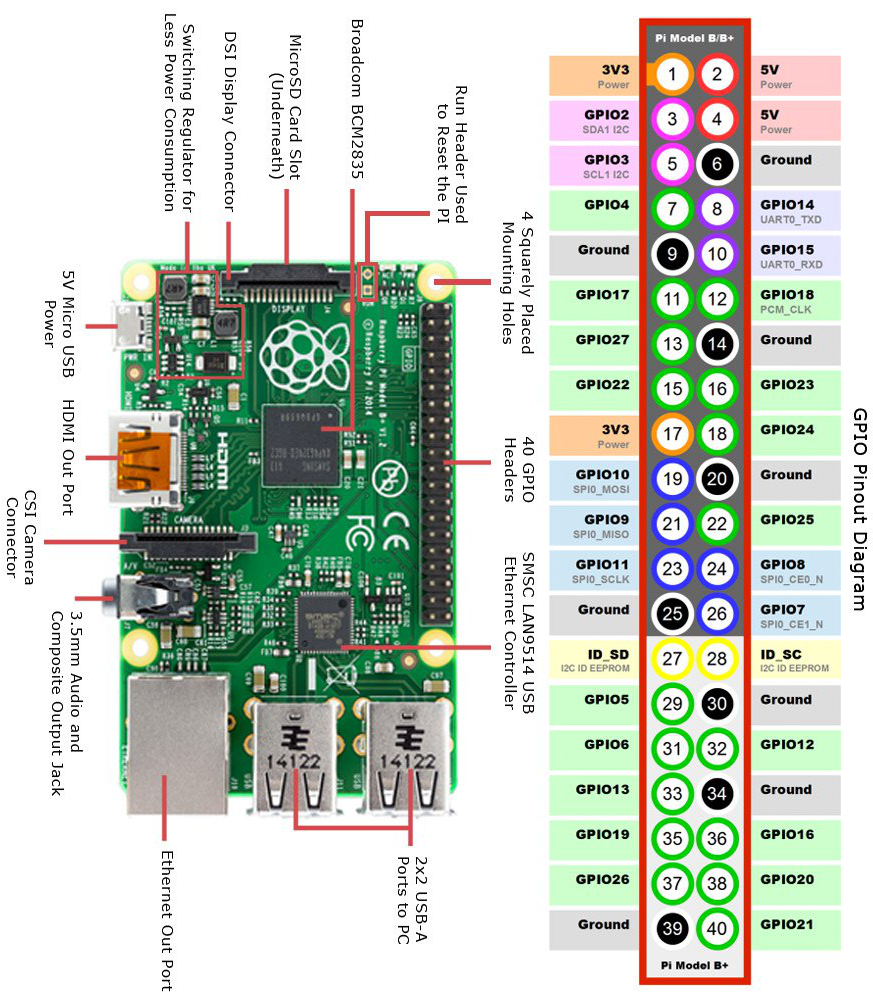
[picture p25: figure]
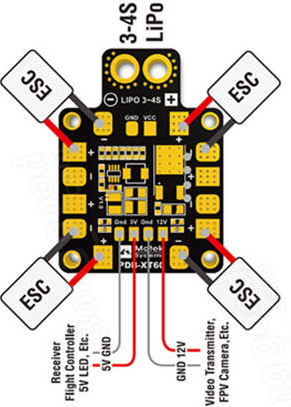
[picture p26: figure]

PDB für mdulares Sensorboard


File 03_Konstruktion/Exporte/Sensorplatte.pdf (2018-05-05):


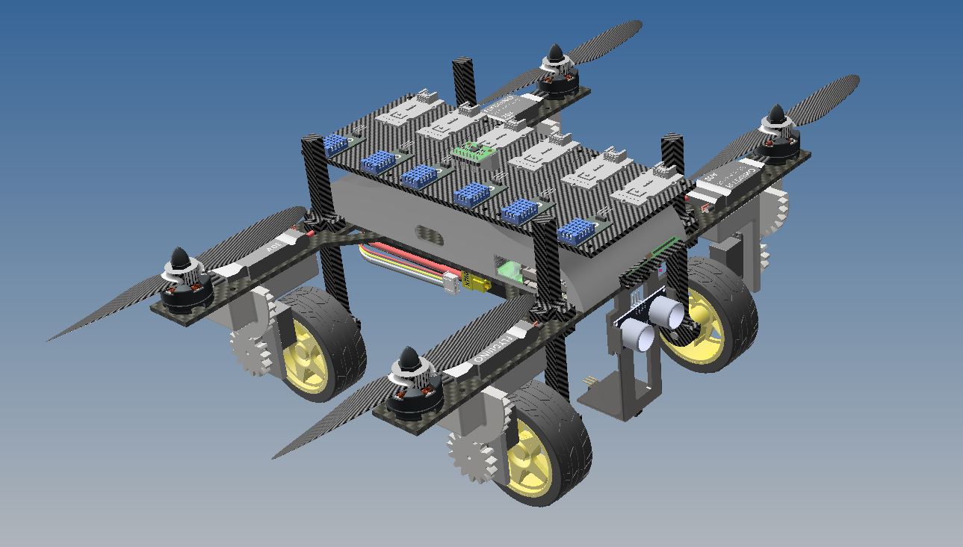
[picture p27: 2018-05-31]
03_Konstruktion/Exporte/ModulareSensorplatte.JPG

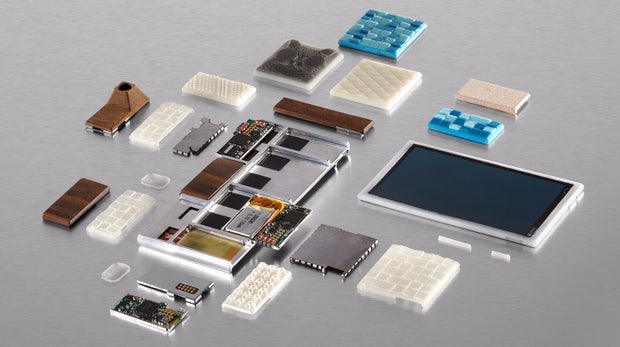
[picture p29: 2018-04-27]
01_Projektmanagement/project-ara-modulare-smartphones-hero.jpg

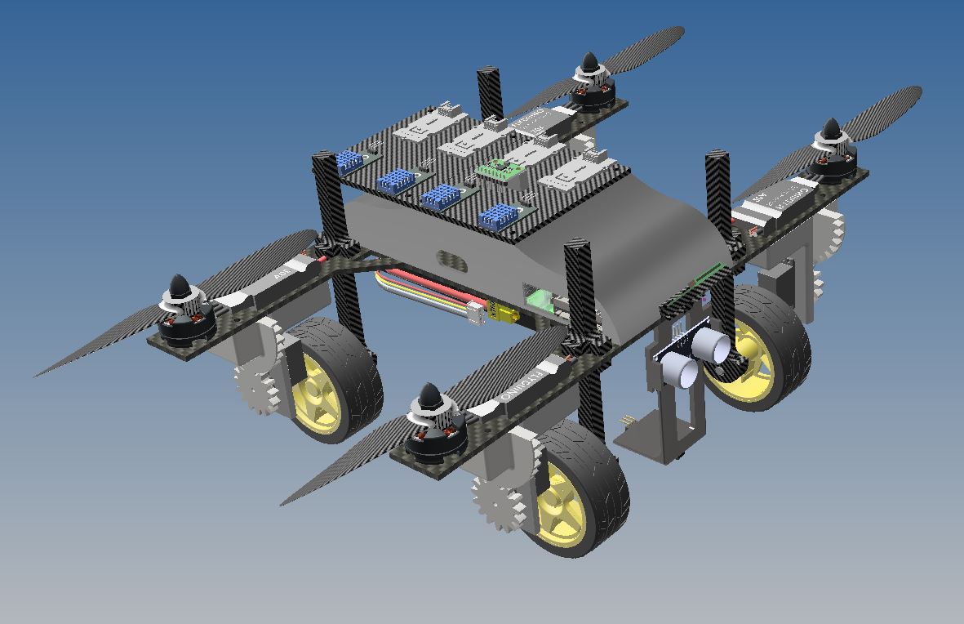
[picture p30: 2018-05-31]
03_Konstruktion/Exporte/ModulareSensorplatte1.JPG

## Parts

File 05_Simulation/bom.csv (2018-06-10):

Name | Quantity | Component
U5 | 1 | Arduino Uno R3
SERVO1 | 1 | Micro Servo
PING1 | 1 | Ultrasonic Distance Sensor
U1 | 1 | Temperature Sensor [TMP36]
Rpot1 | 1 | 250 kOhm, Potentiometer
U2 | 1 | LCD 16 x 2
R1 | 1 | 220 ohm Resistor

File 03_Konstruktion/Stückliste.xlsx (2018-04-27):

Name | Anzahl | Anmerkungen
Chassis mit motorlöcher | 1
Platzhalter Zylinder Klein | 4
Metall Stab M5 | 1
Chassis-2 | 1
Kegelrad | 1
EMax Motor | 4 | STEP AP203
RaspberryPi2 STEP214 | 1 | STEP AP214
Metall Stab M5_MIR | 1
StirnradUNDServo_MIR | 1
Propeller | 4
arduino uno | 1 | SolidWorks IGES file using analytic representation for surfaces
MPU 6050 IMU | 1
Abstandhalter_MPU | 1
LiPo Akku | 1
PDB | 4 | SolidWorks IGES file using analytic representation for surfaces
Ultrasonic Sensor Halterung | 1
USS | 1 | STEP AP214
Wheel ALL | 2
Radaufhängung | 4
Wheel ALL1_MIR | 2
Achse | 2
Kamerahalterung | 1
ESC | 4
M3 Schrauben | 27
M3 Beilagscheiben | 27
M3 Muttern | 27
Raspberry Pi Camera | 1
Stirnzahnrad1 | 2
Stirnzahnrad2 | 2
servo_SM-S2309S | 2

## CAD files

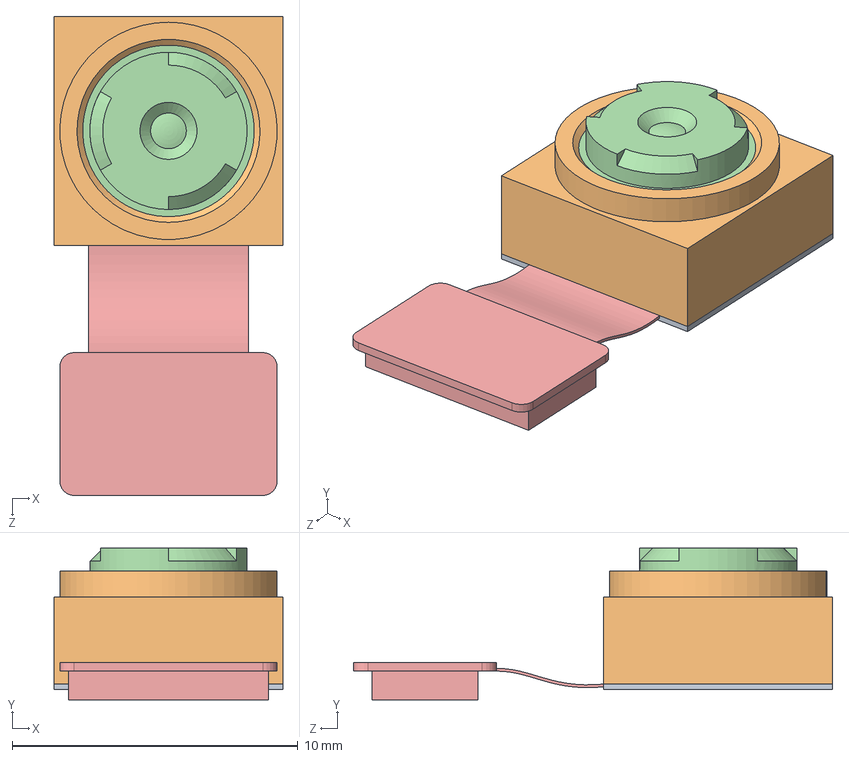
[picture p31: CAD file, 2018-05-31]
03_Konstruktion/OVA5647.SLDASM
8.00 x 5.30 x 16.8 mm
OVA5647
OVA5647_Housing
OVA5647_IR-Glas
OVA5647_Lens
OVA5647_Pigtail

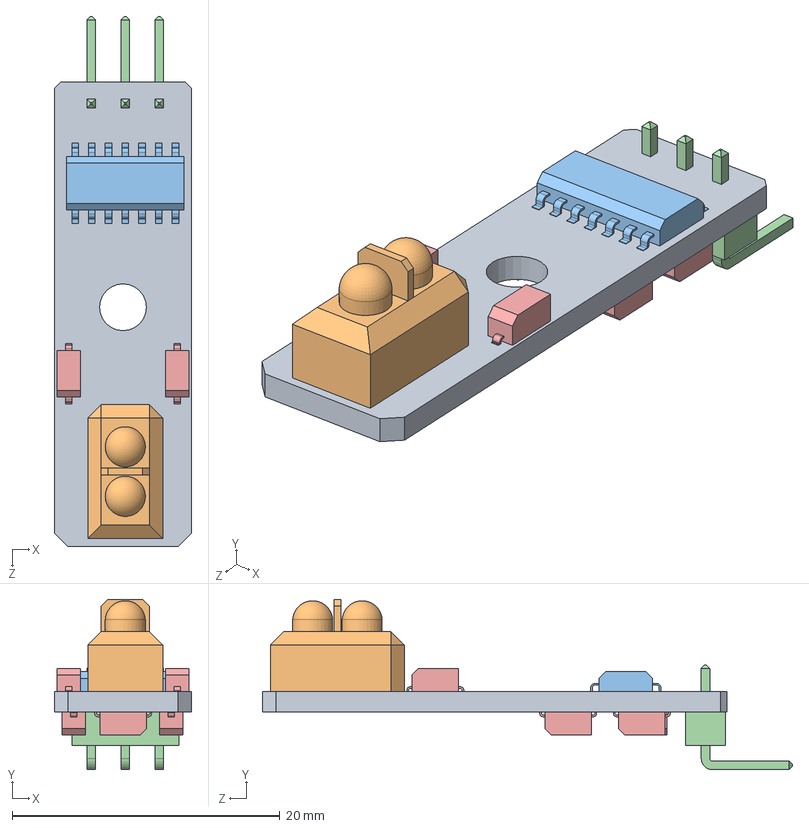
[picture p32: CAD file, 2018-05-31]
03_Konstruktion/Line Sensor.SLDASM
10.2 x 12.7 x 39.6 mm
Line Sensor
TCR5000
14 Pin SMT
3 Pin Header 90 Degree line
Cap1 SMT x 7

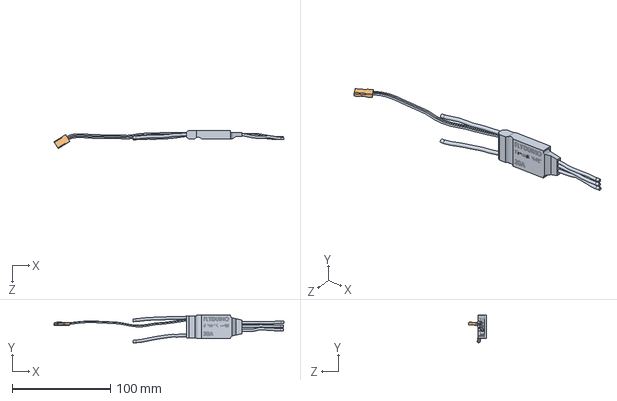
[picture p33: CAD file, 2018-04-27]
03_Konstruktion/28-2-2013-100 - ESC Flyduino SimonK 20A.SLDASM
234.5 x 28.3 x 18.7 mm
28-2-2013-001 - ESC Flyduino SimonK 20A body
28-2-2013-002 - ESC 3-pin connector

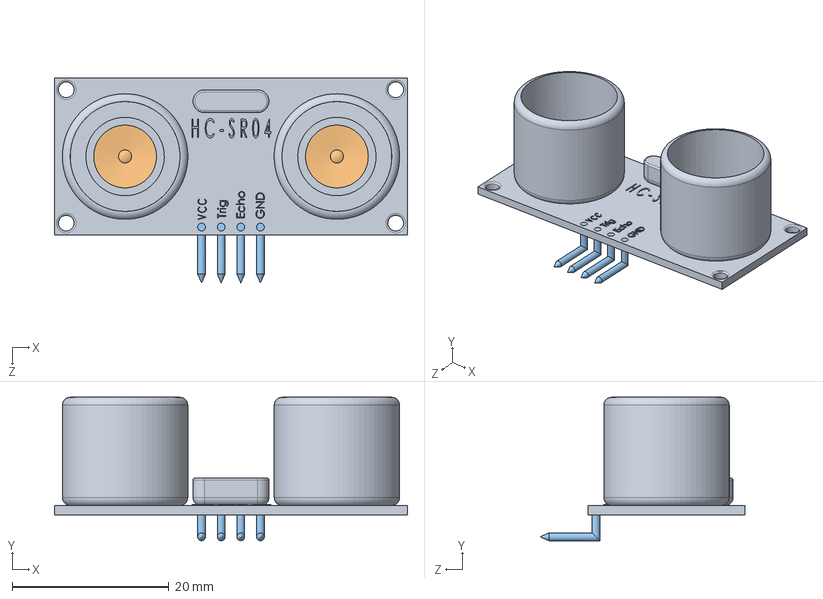
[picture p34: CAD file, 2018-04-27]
03_Konstruktion/Assem3.SLDASM
45.0 x 18.3 x 26.1 mm
UltraSonic
pin header x 4

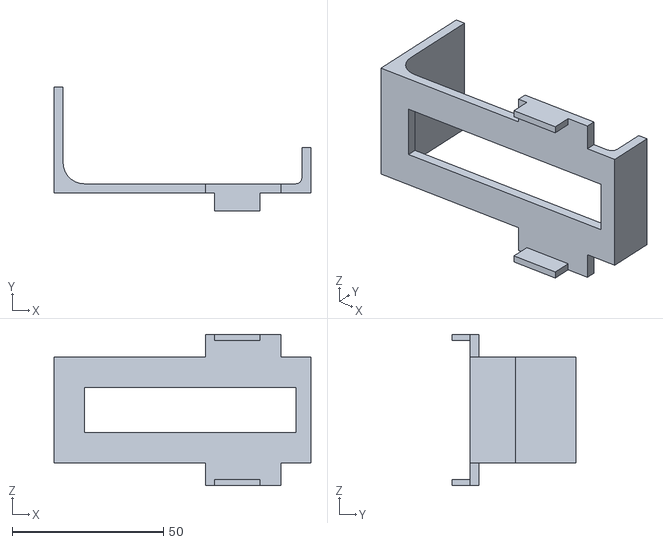
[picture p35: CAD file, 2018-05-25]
03_Konstruktion/Exporte/Ultrasonic.stl
84.9 x 41.0 x 50.0

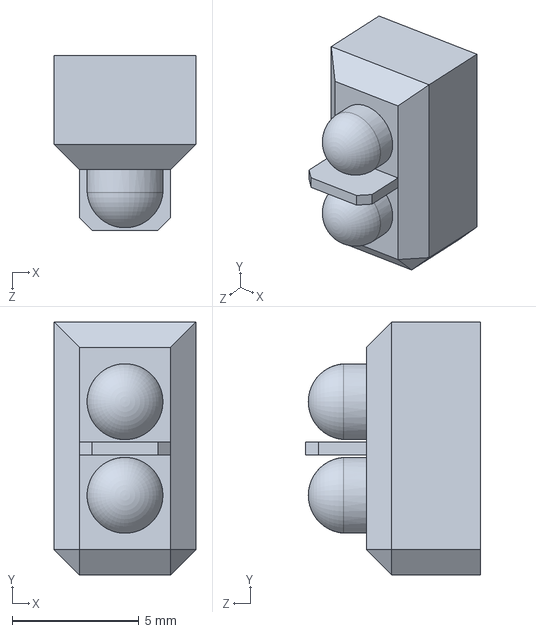
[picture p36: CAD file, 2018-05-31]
03_Konstruktion/TCR5000.SLDPRT
5.60 x 10.0 x 6.90 mm

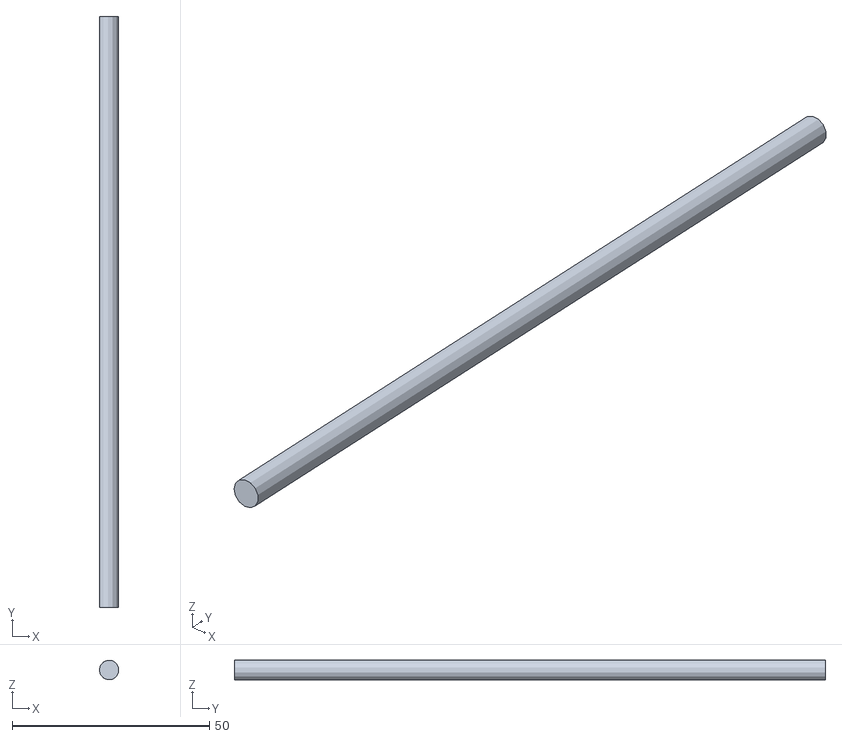
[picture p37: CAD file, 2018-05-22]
03_Konstruktion/Exporte/Achse.stl
4.93 x 150.0 x 4.96

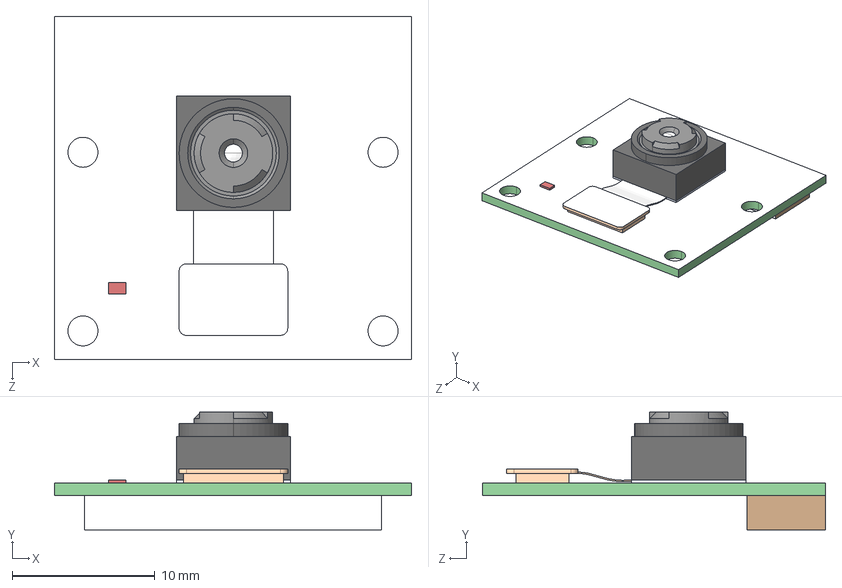
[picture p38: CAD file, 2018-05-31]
03_Konstruktion/RasPi_Camera.STEP
25.0 x 8.25 x 24.0 mm
RasPi_Camera_Board_Standard
OVA5647_Standard
OVA5647_Housing_Standard
OVA5647_IR-Glas_Standard
OVA5647_Lens_FOV
OVA5647_Pigtail_Standard

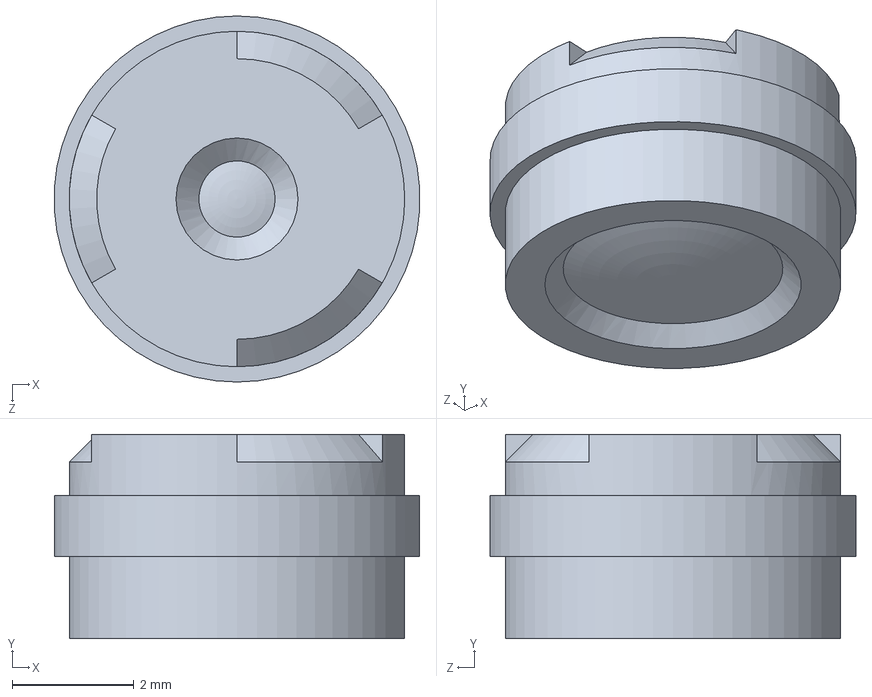
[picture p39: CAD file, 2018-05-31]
03_Konstruktion/OVA5647_Lens.SLDPRT
5.99 x 3.35 x 6.00 mm

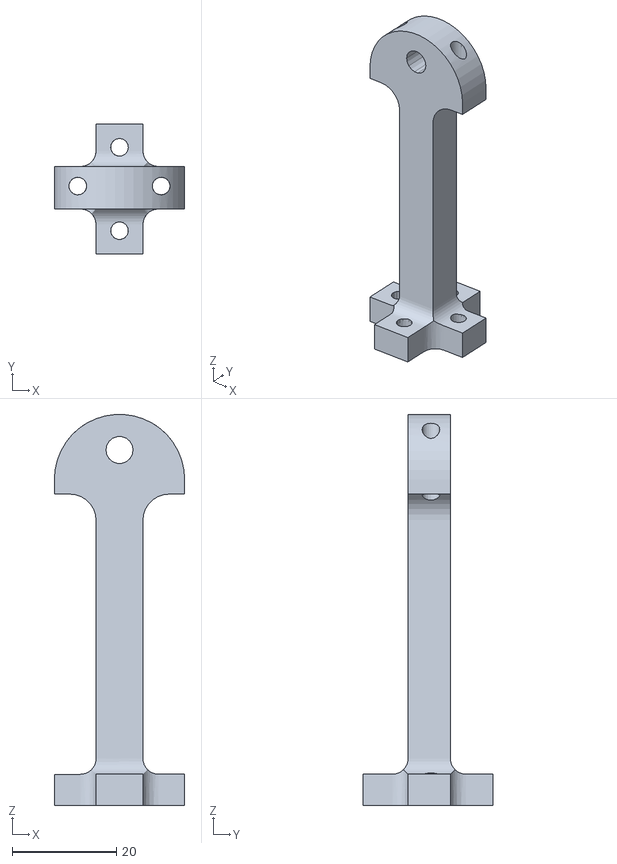
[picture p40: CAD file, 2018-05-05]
03_Konstruktion/Exporte/Radaufhängungneu.STL
25.0 x 25.0 x 75.0

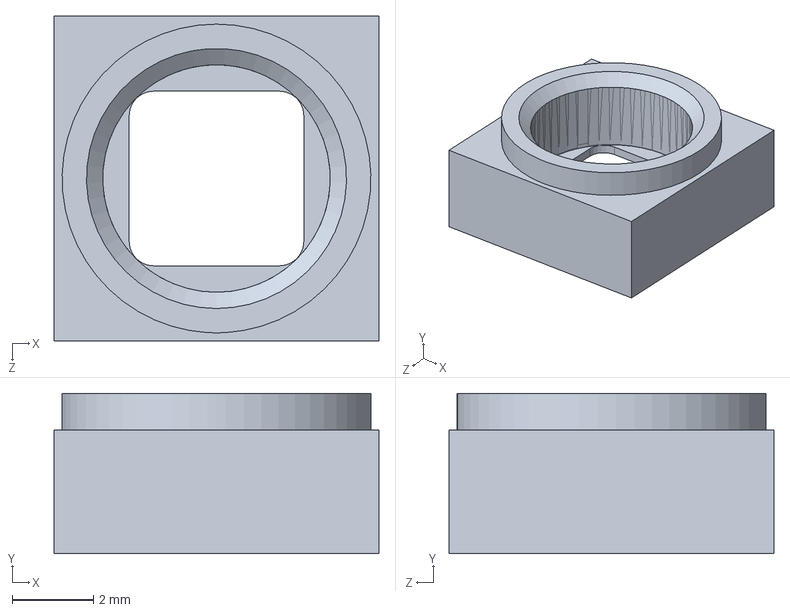
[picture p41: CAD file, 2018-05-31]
03_Konstruktion/OVA5647_Housing.SLDPRT
8.00 x 3.95 x 8.00 mm

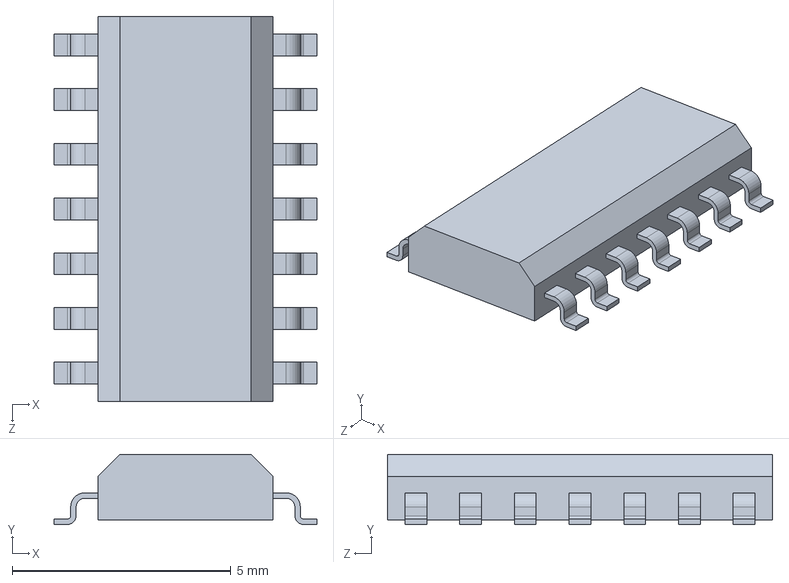
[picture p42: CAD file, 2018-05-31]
03_Konstruktion/14 Pin SMT.SLDPRT
6.00 x 1.60 x 8.80 mm

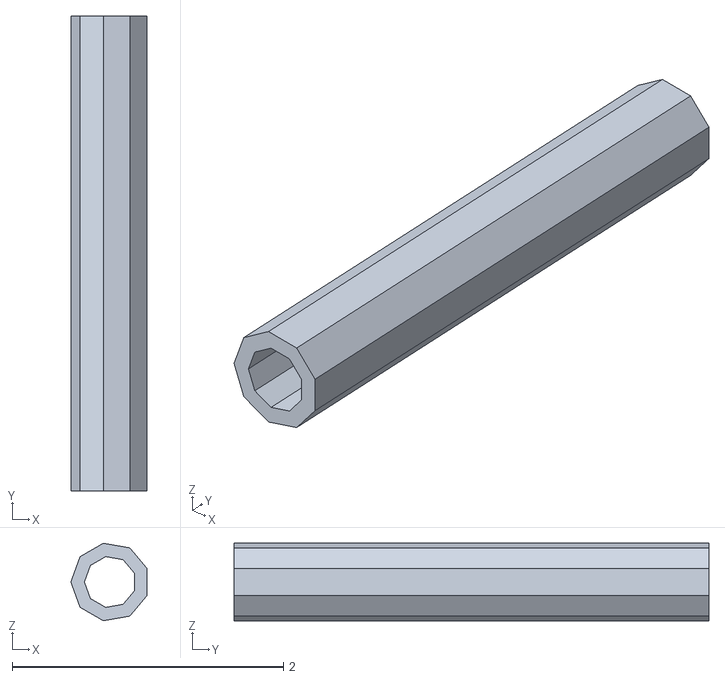
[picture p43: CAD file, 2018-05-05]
03_Konstruktion/Exporte/Platzhalter Zylinder Klein.stl
0.563 x 3.50 x 0.571

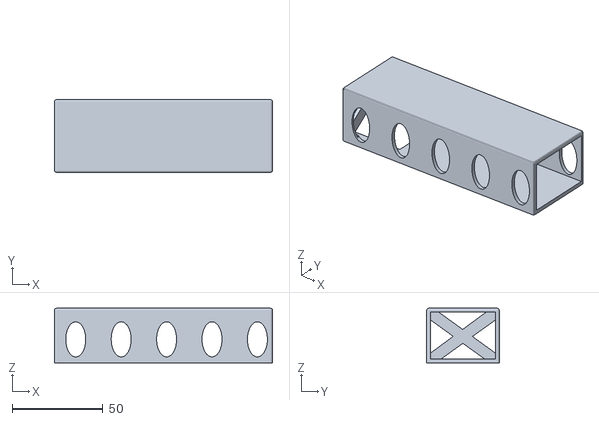
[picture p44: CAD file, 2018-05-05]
03_Konstruktion/Exporte/Akkubox.stl
120.0 x 40.0 x 30.0

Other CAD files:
03_Konstruktion/Exporte/kamera ot.dwg
03_Konstruktion/Exporte/Sensoplatte.dwg
03_Konstruktion/Exporte/chassis mit motorlöcher.dwg
03_Konstruktion/panasonic for mc.SLDPRT
03_Konstruktion/01000A-010-001-PN.ipt
03_Konstruktion/01000A-040-001-SC.ipt
03_Konstruktion/01000A-040-001-UE.ipt
03_Konstruktion/01000A-040-002-LE.ipt
03_Konstruktion/01000A-040-005-MR.ipt
03_Konstruktion/01000A-040-006-RW.ipt
03_Konstruktion/01000A-040-007-CM.ipt
03_Konstruktion/01000A-050-001-BH.ipt
03_Konstruktion/01000A-050-002-BC.ipt
03_Konstruktion/01000A-050-004-SW.ipt
03_Konstruktion/01000A-050-Motor Bearing.iam
03_Konstruktion/28-2-2013-001 - ESC Flyduino SimonK 20A body.SLDPRT
03_Konstruktion/28-2-2013-001 - ESC Flyduino SimonK 20A body.ipt
03_Konstruktion/28-2-2013-001 - ESC Flyduino SimonK 20A body_MIR.ipt
03_Konstruktion/28-2-2013-001 - ESC Flyduino SimonK 20A body_MIR1.ipt
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

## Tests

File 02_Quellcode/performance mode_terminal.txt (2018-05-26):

echo "performance" |sudo tee /sys/devices/system/cpu/cpu0/cpufreq/scaling_governor

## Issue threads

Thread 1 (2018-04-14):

Fernsteuerung Ansteuerung--> Motorsteuerung Max Geschwindigkeit, delay bei Tastendruck, z.B. rechter Pfeil = rechtskurve so lange du hälst etc....

gchrizZz, 2018-04-14:

LudiP, 2018-04-14:
http://www.instructables.com/id/Controlling-a-Raspberry-Pi-RC-Car-With-a-Keyboard/

gchrizZz, 2018-04-28:
https://stackoverflow.com/questions/45584937/how-to-detect-key-release-with-python-not-keypress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

Closed 2018-05-25.

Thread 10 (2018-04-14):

Bilder automatisch uploaden programmieren (optional)

gchrizZz, 2018-04-14:

MaxMoebes, 2018-04-27:
Vorschlag: Bilder pushen über Twitter
http://raspi.tv/2014/taking-and-tweeting-a-photo-with-raspberry-pi-part-4-pi-twitter-app-series

MaxMoebes, 2018-05-04:
Twitter Account: Mohne_2.0

https://twitter.com/0Mohne

LudiP, 2018-05-07:
https://projects.raspberrypi.org/en/projects/magic-8-ball/6

Gute Erklärung um Random Statustexte zu verwenden.
Alternativ können wir auch einen Zähler einbauen der die Anzahl der hochgeladenen Fotos zählt und im Status dann zB sowas steht: 1. Hindernis:  2. Hindernis:  etc...
Bevorzugen würd ich witzige und zufällige Texte :P

MaxMoebes, 2018-05-09:
Hab die random Statustexte in den TwitterPush Code eingebaut. Müssen uns jetzt nur noch was gutes überlegen. für die Statusmeldungen.

Closed 2018-05-25.

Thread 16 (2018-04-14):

Klärungsmail an Hr. Lettnin/ Schmiedinger bzgl. Aufgabenstellung Matlab - BilderUpload + Kein Tutorial...

gchrizZz, 2018-04-14:

ChristophJungwirth, 2018-04-14:
Hallo Herr Lettnin,

wir sitzen gerade bei der Aufgabenteilung in unserem Projekt und sind uns bei folgenden Punkten nicht sicher was damit gemeint ist.

1.	Wie soll Matlab in Bezug auf die Telemetrie-Daten angewendet werden (Wenn überhaupt)?
Sollen wir hier eine Live-Verbindung während der Fahrt darstellen auf einem lokalen Laptop oder über Matlab online? Macht es hier nicht mehr Sinn, mehrere Konten des ThingsSpeak miteinander zu verknüpfen und mit Hilfe von mqtt-Protokoll zu Verknüpfen.
2.	Bei der Hinderniserkennung soll ein Bild vom Hindernis gemacht werden, wo bzw. wie soll dieses den gespeichert werden?
3.	Wie soll die Simulation aussehen? Haben wir hier noch eine Vorlesung?

Über eine schnelle Rückmeldung würden wir uns freuen.

Mit freundlichen Grüßen

Christoph Jungwirth

Closed 2018-04-28.

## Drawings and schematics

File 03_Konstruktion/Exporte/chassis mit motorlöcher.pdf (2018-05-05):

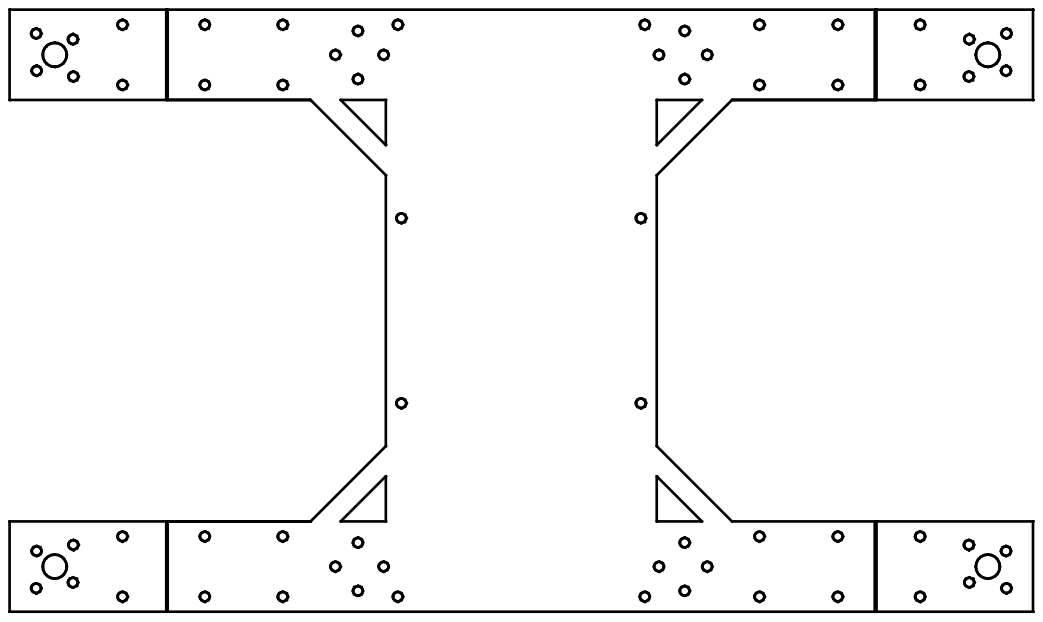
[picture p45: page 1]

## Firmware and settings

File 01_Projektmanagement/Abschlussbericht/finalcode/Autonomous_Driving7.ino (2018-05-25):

//Libraries
#include <SPI.h>
#include <Wire.h>
#include <Adafruit_GFX.h>
#include <Adafruit_SSD1306.h>

//Ultrasonic sensor pins
#define trigPinL 13
#define echoPinL 12
#define trigPinR 2 //vorher A3
#define echoPinR 3
#define trigPinM 10 //vorher A1
#define echoPinM 4 //vorher A2

//Motor pins
#define ENL 5
#define ENR 6
#define IN1 7
#define IN2 8
#define IN3 9
#define IN4 11

//IR sensors pins only for digital use
#define sensorValueR A1
#define sensorValueM A2
#define sensorValueL A3
long sensors_average;
int sensors_sum;
int posi;
int IRSensor[3]={0, 0, 0};

//Display
#define OLED_RESET 0
Adafruit_SSD1306 display(OLED_RESET);

void setup() {
  Serial.begin (9600);
// setup ultrasonic sensors
  pinMode(trigPinL, OUTPUT);
  pinMode(echoPinL, INPUT);
  pinMode(trigPinR, OUTPUT);
  pinMode(echoPinR, INPUT);
  pinMode(trigPinM, OUTPUT);
  pinMode(echoPinM, INPUT);
//setup ir sensors only for digital use
  //pinMode(sensorValueL,INPUT);
  //pinMode(sensorValueR,INPUT);
  //pinMode(sensorValueM,INPUT);
//setup display
  display.begin(SSD1306_SWITCHCAPVCC, 0x3C); //initialize with the I2C addr 0x3C (128x64)
  display.clearDisplay();
//setup motors 
  pinMode(IN1, OUTPUT);
  pinMode(IN2, OUTPUT);
  pinMode(IN3, OUTPUT);
  pinMode(IN4, OUTPUT);
//setup "speedPins"
  pinMode(ENL, OUTPUT);
  pinMode(ENR, OUTPUT);
}

//MotorSpeed should be at least 100
int max_speed = 120;
int motorSpeedL = 0;
int motorSpeedR = 0;

//initialize distance with 0
int distanceL = 0, distanceR = 0, distanceM = 0;

//initializse PID variables
float  proportional=0.0;
float  integral=0.0;
float  derivative=0.0;
float  Kp=150.0;
float  Ki=0.15;
float  Kd=100.0;
float  error_value=0.0;
float  last_proportional=0.0;

//initialize ir sensor values
int irthreshold = 220;
int irthresholdR = 630;// extra Schwellle für rechten Sensor, da der anscheinend defekt ist und Schmarrn misst.
int irthresholdL = 615;// extra Schwellle für rechten Sensor (in zusammenhang mit linkem Sensor), da der anscheinend defekt ist und Schmarrn misst.

//forward
void forward(){ 
  analogWrite(ENL, motorSpeedL+110);
  analogWrite(ENR, motorSpeedR+110);
  digitalWrite(IN1, HIGH);
  digitalWrite(IN2, LOW);
  digitalWrite(IN3, LOW);
  digitalWrite(IN4, HIGH);
  Serial.println("Forward");//debug
}

//back
void back() {
  analogWrite(ENL, motorSpeedL+130);
  analogWrite(ENR, motorSpeedR+130);
  digitalWrite(IN1, LOW);
  digitalWrite(IN2, HIGH);
  digitalWrite(IN3, HIGH);
  digitalWrite(IN4, LOW);
  Serial.println("Back");
}

//left
void left() {
  analogWrite(ENL, motorSpeedL+150);
  analogWrite(ENR, motorSpeedR+30);
  digitalWrite(IN1, HIGH);//
  digitalWrite(IN2, LOW);
  digitalWrite(IN3, LOW);//
  digitalWrite(IN4, HIGH);
  Serial.println("Left"); //debug
}

//right
void right() {
  analogWrite(ENL, motorSpeedL+30);
  analogWrite(ENR, motorSpeedR+150);
  digitalWrite(IN1, HIGH);//
  digitalWrite(IN2, LOW);
  digitalWrite(IN3, LOW);//
  digitalWrite(IN4, HIGH);
  Serial.println("Right");//debug
}

//Pointturn left
  void PTleft() {
  analogWrite(ENL, motorSpeedL+180);
  analogWrite(ENR, motorSpeedR+180);
  digitalWrite(IN1, LOW);
  digitalWrite(IN2, HIGH);
  digitalWrite(IN3, LOW);
  digitalWrite(IN4, HIGH);
  Serial.println("PTLeft"); //debug
}

// Pointturn right
void PTright() {
  analogWrite(ENL, motorSpeedL+180);
  analogWrite(ENR, motorSpeedR+180);
  digitalWrite(IN1, HIGH);
  digitalWrite(IN2, LOW);
  digitalWrite(IN3, HIGH);
  digitalWrite(IN4, LOW);
  Serial.println("PTRight");//debug
}

//stop
void stop() {
  digitalWrite(ENL, LOW);
  digitalWrite(ENR, LOW);
  Serial.println("Stop!");//debug
} 

//Ultrasonic distance measurement functions 
int distance_measureL(){
  float durationL, distanceL; 
  digitalWrite(trigPinL, LOW);
  delayMicroseconds(2); 
  digitalWrite(trigPinL, HIGH);
  delayMicroseconds(10); 
  digitalWrite(trigPinL, LOW);
  durationL = pulseIn(echoPinL, HIGH);
  distanceL = (durationL/2) / 29.1;
    return (int)distanceL;
  }
  
int distance_measureR(){
  float durationR, distanceR;  
  digitalWrite(trigPinR, LOW);
  delayMicroseconds(2); 
  digitalWrite(trigPinR, HIGH);
  delayMicroseconds(10); 
  digitalWrite(trigPinR, LOW);
  durationR = pulseIn(echoPinR, HIGH);
  distanceR = (durationR/2) / 29.1; 
  return (int)distanceR;
  }

int distance_measureM(){
  float durationM, distanceM;  
  digitalWrite(trigPinM, LOW);
  delayMicroseconds(2); 
  digitalWrite(trigPinM, HIGH);
  delayMicroseconds(10); 
  digitalWrite(trigPinM, LOW);
  durationM = pulseIn(echoPinM, HIGH); 
  distanceM = (durationM/2) / 29.1;  
  return (int)distanceM;
  }

//sensor read
void readIRSsensors()
{
sensors_average = 0;
sensors_sum = 0; 
for (int i = 0; i < 3; i++){
IRSensor[i] = analogRead(i);
sensors_average += IRSensor[i] * i * 1000;   
sensors_sum += int(IRSensor[i]);}
posi = int(sensors_average / sensors_sum);
/*
Serial.print(sensors_average);
Serial.print(" sensors_average ");
Serial.print(sensors_sum);
Serial.print(" sensors_sum ");
Serial.print(posi);
Serial.print(" posi ");
Serial.println();
//delay(1000);
*/
}

//PID calculation, for better motorcontrol
void calculatePID()
{
posi = int(sensors_average / sensors_sum);
proportional = float(posi - 11);
integral = (integral + proportional);
derivative = proportional - last_proportional;
last_proportional = proportional;
error_value = int(proportional * Kp + integral * Ki + derivative * Kd);

/*Serial.print(posi);
Serial.print(" posi ");
Serial.print(proportional);
Serial.print(" proportional ");
Serial.print(integral);
Serial.print(" integral ");
Serial.println();
Serial.print(derivative);
Serial.print(" derivative ");
Serial.print(last_proportional);
Serial.print(" last_proportional ");
Serial.println();
Serial.print(error_value);
Serial.print(" error_value ");
Serial.println();
//delay(2000);
*/
}

//calculate motorturns
void motorturn(){  //Restricting the error value between +255.
if (error_value< -120){ error_value = -120;     } if (error_value> 120){
error_value = 120;
    }
 
// If error_value is less than zero calculate right turn speed values
if (error_value< 0){
motorSpeedR = max_speed + error_value;
motorSpeedL = max_speed;
Serial.println("Right"); //debug
    }
 
// Iferror_value is greater than zero calculate left turn values
 
else{
motorSpeedR = max_speed;
motorSpeedL = max_speed - error_value;
Serial.println("Left"); //debug
    }
}

//PID controled motorspeed
void motor_drive(int motorSpeedR,int motorSpeedL){
analogWrite(ENR, motorSpeedR);
analogWrite(ENL, motorSpeedL);
  digitalWrite(IN1, HIGH);
  digitalWrite(IN2, LOW);
  digitalWrite(IN3, LOW);
  digitalWrite(IN4, HIGH);
}

//////////////////////////////////////////////Mainloop//////////////////////////////////////////////////////
void loop() {
//Write distances into their variables, by getting them from the function
distanceL = distance_measureL();
distanceR = distance_measureR();
distanceM = distance_measureM();
  
//Initialize Display, by cleaning it up
    display.clearDisplay();
    
//Show dinstanceL = left ultrasonic sensor  
    display.setCursor(25,5);
    display.setTextSize(2);
    display.setTextColor(WHITE);
    display.println(distanceL);
    display.setCursor(60,5);
    display.println("cm");
    display.setCursor(5,5);
    display.println("L");
    display.display();
    
//Show distanceR = right ultrasonic sensor
    display.setCursor(25,25);
    display.println(distanceR);
    display.setCursor(60,25);
    display.println("cm");
    display.setCursor(5,25);
    display.println("R");
    display.display();

//Show distanceM = middle ultrasonic sensor
    display.setCursor(25,45);
    display.println(distanceM);
    display.setCursor(60,45);
    display.println("cm");
    display.setCursor(5,45);
    display.println("M");
    display.display();
/*
//Show ir sensors on oled
  if((digitalRead(sensorValueR))==LOW){
    display.setTextSize(2);
    display.setTextColor(WHITE);
    display.setCursor(85,5);
    display.println("IRL");
    display.display();
    Serial.println(sensorValueR);
  }
    //mit analog werten if((irthresholdL<IRSensor[0])&& (irthreshold<IRSensor[0])&&(IRSensor[0]<irthresholdR)){
    if((digitalRead(sensorValueL))==LOW){
    display.setTextSize(2);
    display.setTextColor(WHITE);
    display.setCursor(85,25);
    display.println("IRR");
    display.display();
    Serial.println(sensorValueL);
  }
    if((digitalRead(sensorValueM))==LOW){
    display.setTextSize(2);
    display.setTextColor(WHITE);
    display.setCursor(85,45);
    display.println("IRM");
    display.display();
    Serial.println(sensorValueM);
  }
  */
//here starts the magic ;-)
//on the line
/*if ((((digitalRead(sensorValueR))==HIGH) || ((digitalRead(sensorValueL))==HIGH) || ((digitalRead(sensorValueL))==HIGH)) && ((distance_measureL()>25 || distance_measureR()>15 || distance_measureM>12))){
  readIRSsensors();
  calculatePID();    
  motorturn();
  motor_drive(motorSpeedR,motorSpeedL);
}
else if (distance_measureL()<8 || distance_measureR()<8 || distance_measureM()<10)
      {
      stop();
      if (distance_measureL() > distance_measureR())
      PTleft();
      if (distance_measureL() < distance_measureR())
      PTright();
      } 
      */ 
//beside the line
if (distanceL>15 && distanceR>12 && distanceM>10){
forward();
}
if (distanceL<15 && distanceR>12 && distanceM>10){
left();
}
if (distanceL>15 && distanceR<12 && distanceM>10){
right();
}
//Emergencystop beside the line
if (distanceL<10 || distanceR<10 || distanceM<10)     
      {
      stop();
      delay(50);
      if (distanceL > distanceR)
      PTleft();
      delay(150);
      if (distanceL < distanceR)
      PTright();
      delay(150);
      }
if (distanceL<5 || distanceR<5 || distanceM<5)      
      {
      stop();
      back();
      delay (50);
      }  
}

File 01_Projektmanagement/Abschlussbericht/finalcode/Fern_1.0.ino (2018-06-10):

#include <Servo.h>
#include <Wire.h>
#define SLAVE_ADDRESS 0x04
//motor 2 links vorne
//motor 1 rechts vorne
//motor 3 rechts hinten
// motor 4


int motor1_A=11; 
int motor1_B=10;
int motor1_Speed=9;

int motor3_Speed=2;
int motor3_B=4;
int motor3_A=7;

//int motor4_Speed=;
//int motor4_B=;
//int motor4_A=;

int motor2_A=6;
int motor2_B=5;
int motor2_Speed=3;

char number[50]; //ka wieso^^

void receiveData(int byteCount) {
  while (Wire.available()) {
    int number = Wire.read();
    if (number == 1){    //vorne
     Fahren();  
     }
    if (number == 2){
    Rechts();
    }
    if (number == 3){   //links
    //digitalWrite(4, HIGH);
     Links();
    }
    if (number == 4){  //hinten
    //digitalWrite(2, HIGH);
   // Serial.print (number);
   Hinten();
    }
    if (number == 5){   //keininput
      Stop();
     
    }
  }
   
 }
void Fahren(){   
   digitalWrite(motor1_A,HIGH); 
   digitalWrite(motor1_B,LOW);
   digitalWrite(motor2_A,LOW); 
   digitalWrite(motor2_B,HIGH);
   analogWrite(motor1_Speed,255);
   analogWrite(motor2_Speed,255);
  }
void Rechts(){ 
    analogWrite(motor1_Speed,255);
    analogWrite(motor2_Speed,255);
    digitalWrite(motor1_A,HIGH); 
    digitalWrite(motor1_B,LOW);
    digitalWrite(motor2_A,HIGH); 
    digitalWrite(motor2_B,LOW);
}
void Hinten(){
  analogWrite(motor1_Speed,255);
  analogWrite(motor2_Speed,255);
  digitalWrite(motor1_A,LOW);
  digitalWrite(motor1_B,HIGH);
  digitalWrite(motor2_A,HIGH);
  digitalWrite(motor2_B,LOW);
}

void Links(){ 
   analogWrite(motor1_Speed,255);
  analogWrite(motor2_Speed,255);
  digitalWrite(motor1_A,LOW);
  digitalWrite(motor1_B,HIGH);
  digitalWrite(motor2_A,LOW);
  digitalWrite(motor2_B,HIGH);
}
void Stop(){
  analogWrite(motor1_Speed,0);
  analogWrite(motor2_Speed,0);
  digitalWrite(motor1_A,LOW);
  digitalWrite(motor1_B,LOW);
  digitalWrite(motor2_A,LOW);
  digitalWrite(motor2_B,LOW);
}
void setup(){
  Serial.begin(9600);
  Serial.setTimeout(500);
  Wire.begin(SLAVE_ADDRESS);
  Wire.onReceive(receiveData);
  pinMode(motor1_A,OUTPUT);
  pinMode(motor1_B,OUTPUT);
  pinMode(motor2_A,OUTPUT);
  pinMode(motor2_B,OUTPUT);
  Serial.begin (9600);
 }


void loop() {
  // delay(100);
    //Hinten();
    //Stop();



}

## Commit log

2018-04-27 Fertigstellung Konstruktion
    [01000A-010-001-PN.ipt, 01000A-040-001-SC.ipt, 01000A-040-001-UE.ipt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]
2018-05-05 Add files via upload
    Pi code für i2c senden der WASD steuerung
2018-05-19 Add files via upload
    Fernbedienung, i2c, Foto Twitter
2018-05-22 Achse nachkonstruiert
    [Achse.0002.ipt, Achse.ipt, Achse.stl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]
2018-05-25 Quellcode für Auto
    [Ultrasonic.stl]
2018-05-31 Designüberarbeitung
    [14 Pin SMT.SLDPRT, 28-2-2013-001 - ESC Flyduino SimonK 20A body.ipt, 28-2-2013-001 - ESC Flyduino SimonK 20A body_MIR.ipt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]
2018-06-09 Arduino Fernsteuerung
2018-06-10 Projektbericht meinen Teil fertiggestellt und als gesondertes Dokument hochgeladen. Ich habe aber das aktuellste Dokument genommen, es kann also auch mit meinem weitergemacht werden.
